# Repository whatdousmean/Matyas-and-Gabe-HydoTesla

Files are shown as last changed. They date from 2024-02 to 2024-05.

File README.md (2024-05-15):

# HydroTesla - Gabe Syring and Matyas Velgersdyk - May 15, 2024
Figure 1 - Final Product

Figure 2 - Water Board
WaterBoard
Figure 3 - Main Circuit
MainCircuit
Figure 4 - Photoresistor Headlights
Headlights
Figure 5 - Full Circuit (Main, photoresistors, and LED circuit all combined)
FullCircuit
Figure 6 - Back axel connected to gear shaft and motor
BackAxel
Figure 7 - Circuit Schematic
CircuitSchem
Figure 8 - LED Circuit
LED
Figure 9 - Battery
battery
Figure 10 - Battery Plug
batteryconnect
Figure 11 - Battery Holder
batteryPlace
Figure 12 - Finished Chassis
chassis
Figure 13 - Front Axel
frontAxel
Figure 14 - Motor & Custom Motor Holder
motor
Figure 15 - Servo
servo
Figure 16 - Blueprint
blueprint

# Design Summary
This is a car that is powered by a 12 volt battery. The battery current flows through a mosfet gateway, that can be opened by the 12 pin on an arduino uno being powered. That 12 pin is powered when our water board is put into water, stored in a tupperware container near the center of the car. That water board sends a signal back to the A0 pin on the arduino. If that analogRead value is over 150, the 12 pin will be powered, allowing the circuit to be completed, powering our 12 volt motor. This motor is connected to a simple gear system near the back of the car that is also attached to our back axel. When the motor turns, so does the axel. At the front of the car, there are two "headlights". These "headlights" are mini photoresistor circuits. Both of these circuits are powered through 5 volt pins on the arduino, and they feature voltage dividers. These voltage dividers split the current to ground and an analog pin. These two pin values are read, and then transferred into a servo. This servo is connected to our specially designed front axel, capable of performing front-steering based off of the direction of the servo. The arduino is coded to specific standards with these photoresistors. The requirements for the servo to turn are as follows: 
1) The motor must be running (The water board must be in water).
2) The analogRead value returned by one photoresistor circuit must be higher than the other.
3) The value must be higher than 150.

If all of these requirements are met, the servo will turn to either 57.5 or 122.5 degrees. This is determined by if the photoresistor is on the left or right. Otherwise, the servo remains at 90 degrees, allowing for the car to be straight. Finally, when the water board is active, it also activates the 9 pin on the arduino, turning on a green LED on the top of the car. This is just a signal showing that the car is on.

# System Details
## Main Circuit
The main circuit features a mosfet gateway that is activated from pin 12. Pin 12 is turned on by the analogRead function coming from the water board. Our circuit also features other small things, like resistors and a diode. A picture of the main circuit with the headlights and LED connected can be found in **Figure 5**.
## Water Board
Our water board is attached to the A0 pin. This pin gets a value from the water board through the analogRead() function. If the analogRead value is over 150, it activates the 12 pin, turning on the mosfet gateway. This allows the circuit to be completed, and the motor to move. The motor makes the car move because it is connected to the back axel via a gear system. A picture of the water board can be found in **Figure 2**.
## Motor
Our motor is powered through our main circuit once the mosfet gateway is activated. It is located underneath the car. We designed a custom motor holder for this, and used zipties and screws to hold it in place. A picture of the motor, gear shaft, and back axel can be found in **Figure 6**.
## Photoresistor Headlights
Our photoresistor headlights have a voltage divider on the back end of them. This splits the voltage to ground and to an analogRead() pin (Pins A1 and A2). If either these values are above 150, the 3 pin will activate using the myservo.write() function, turning the servo to the desired degree. A picture of the headlights can be found in **Figure 4**.
## Servo System
Once the 3 pin sends the servo a signal through the myservo.write() function, the servo turns to the desired degree. (For our project those degrees are 90, 57.5, and 122.5).
## LED Circuit
When the water board is activated by water, the 9 pin is turned on. This is connected to a simple LED circuit. It's only purpose is to be an on/off indicator. A picture of the LED circuit can be found in **Figure 8**.
## Battery
We used a 12 volt battery, found in the robotics lab. We used anderson power pole connectors to connect the battery to the circuit, and electical tape to secure the connection. Pictures of this can be found in **Figures 9, 10, and 11**.
## Wiring Diagram
**A detailed schematic of our wiring systems can be found in Figure 7**

# Design Evaluation
  ## Output Display 
  We used a singular green LED on the top of the car to show if it was on or off. It is powered by the 9 pin, which is turned on when the water board is dipped in water.
  ## Manual User Input 
  Our manual user input is in the form of our photoresistor headlights. The user shines a light at either of the headlights, and the car will turn towards the light.
  ## Automatic Sensor 
  Our water board automatically senses if there is water on it or not. If there is, the water board will activate our 12 volt motor and green LED. If not, the car will remain stationary and the LED will be off.
  ## Actuators 
  We used two different actuators, our servo, which activated our front steering, and a 12 volt motor, which powered the back axel to spin, and thus, the car to move.
  ## Mechanisms 
  Our two main mechanisms were our gear shaft that connected our motor to the back axel, and the servo's connection to the front axel to determine steering.
  ## Hardware 
  We had lots of different hardware, so here are all of the items: Arduino uno, plywood, screws, bolts, axels, wheels, motor, servo, tupperware, wires, CUSTOM 3D PRINTED MOTOR HOLDER, resistors, photoresistors, mosfet, LED, water board, breadboard, CUSTOM PRINTED GEARS

  Link to gear STL file: https://github.com/whatdousmean/Matyas-and-Gabe-HydroTesla/blob/ece42019ce43cfadcfe1f235608ce2f768c4addd/Main%20Gear.stl
  ## Logic, Processing, and Control
  Our full Arduino Uno code can be found here:
  
  https://github.com/whatdousmean/Matyas-and-Gabe-HydroTesla/blob/e636a06a375cc82a635ebf0bc8ff4fe23f6c6746/Water%20Board%20Arduino%20Code

  Our arduino uno was the main part of this entire project. It enabled everything, the water board, motor, photoresistors, servo, and more to work together. It is important to note that we imported the Servo library into our code in order to be able to use our servo properly. This line where we import the Servo library is on line 2 of our code. 

  ## Other Adjustments
  We did not have very many adjustments to our final plan, just two main ones:

  1) Originally, we had planned to add another photoresistor to determine speed. Unfortunately, we had to cancel this plan due to already low speeds and high resistance from the photoresistor.
  2) While this may not be a real "adjustment" this is important. We designed a custom motor holder that we installed underneath the car. This holds our motor steady and in place. The link to the stl file of this can be found here:
     
     https://github.com/whatdousmean/Matyas-and-Gabe-HydroTesla/blob/3997745cd45f1ab076b2cb9a97db56c113268df8/Custom_Motor_Holder.stl

## Construction, Quality, Aesthetics, and Visual Appeal

We worked down to the last minute on this project, and unfortunately did not have time to make it look very nice.

## Level of Effort

We put numerous out of class hours into this project, and worked down to the very last minute on it. We think we will get extra points for this.

## Cost

Our cost is below $100. We think we will get the extra points for this as well.

# Lessons Learned

Our main lesson that we learned is to be calm. At many points, we got very frustrated. This hindered our work time usage, mood, and overall production. We had many issues building our circuits and getting everything to work together. In the end, staying calm and trying new methods is what enabled us to finish on time. 

Throughout this project, we learned that planning how to use your time is very important. Time flies when you are so focused on something. The class periods went by a lot faster than we expected.

Biggest Suggestion: Plan out your class periods, when you expect to have certain things done by, and stick too it. In February it seemed like we had all the time in the world. Time flies with this project. Stay calm when working, and don't give up.

# Parts List
-Wheels: 8.99 https://www.amazon.com/Electric-Geared-Magnetic-Gearbox-Plastic/dp/B098PZF2DV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

-Tupperware: 4.99 https://www.amazon.com/GladWare-Everyday-Rectangle-Storage-Containers/dp/B0085UK4GW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

-Nuts, Bolts(1/4 inch diameter, 2.5 inch length, 13 count), Washers and Axel : Aprox. 17.50 (Tax Included) at Ace

-Plywood: 10.00

-12 Volt Motor: 14.99 https://www.amazon.com/Greartisan-Electric-Reduction-Centric-Diameter/dp/B07K9KPDNV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

-Arduino: 15.00

-General Electronics(Including Servo, Water Board, and Battery): Aprox. 20.00
	- 4 220 Ohm resistors, mosfet, diode, LED, breadboards

-3d Prints: Motor Casing (50 grams) Beveled Gears (29 grams)

### Total: $91.47
## Other Parts
- Wires
- 3D Printer
- Arduino app
- Connection cords
- Electical tape
  
# Assembly Instructions
If you want to build this, follow these instructions!
## Electronics
The electronic and coding portions of this project are very complicated. Start by copying our code (In logic, processing, and control) over to your arduino script. Also make sure you have all the materials listed. You will need many male to male and male to female wires for this. 

### Circuits
In **Figure 7**, you can see all of the circuit's wiring. Start by building all of these circuits. Put the main circuit on a big breadboard, and the other 3 on mini breadboards. The servo and waterboard do not need a breadboard, you can directly connect them. Make sure to not take off the bottom stickers to these breadboards yet. Throughout building these parts, make sure you are testing voltage and amperage levels with a multimeter. All of this, including the arduino should be powered by the 12 volt battery. Tip: Connect the main power from the battery to the + strip on the main breadboard. From there, power the arduino and the rest of the circuits from the arduino. You will most likely need an arduino shield to have enough ports. A picture of our final circuit can be found in **Figure 5**.

## 3D Printed Parts
We used OnShape to print our **3** custom parts. Download our STL files above and 3D Print these parts. (You will need to print two of the gears).

## Chassis (Main Body), Servo, and Axels

### The chassis blueprints can be found in **Figure 16**.

Before the chassis was constructed, it was planned out on a 3d modeling software used by Geomatic Engineers, colloquially called Surveyors, known as Autodesk Civil 3d. The chassis was modeled after a Ford F150 outline from the top, and although plans were made to make layers to build out the full body shape of the Ford truck, that was never done as it would have taken far too long. Instead, 2 layers, identical for the most part excluding some minor changes surrounding the front wheel wells, and the motor-casing attachment point and cutout. 

After the chassis was designed, it was printed full-scale onto a sheet of paper, and traced onto a sheet of plywood. It was then cut out, excluding the cutouts for the motor casing and the water tank(tupperware container) making use of a scroll saw. After that was done, holes were drilled for support posts between the two chassis layers (the bolts), and the first assembly was done. These bolts at the time were 1.5 inches in length, but after being discovered to be too short later on, they were changed to be 2.5 inches long. In any case, once this was done, focus switched to the steering mechanism and the back axel. 
	
The steering mechanism is made up of two thin cutouts of plexiglass spanning across two free-spinning armistices(a y-shaped aluminum object with a bearing) holding the wheels onto a fixed point, which will be explained in more depth during the presentation. These are then connected to a servo using more free spinning attachment points, to enable easy rotation, and precise control. This was made using the scroll saw and the drill press over the course of a couple of class periods, and was swiftly assembled. The rear axle was much simpler, only making use of 1 beveled gear(3d printed, model lifted from a beveled gear found in the lab) that interfaces with one attached to the motor, a dowel rod, and two wheels,  as well as two pillow blocks to keep the axle in place. To attach the wheels to the axel, the gear was first slid onto the dowel rod after which point I stuck the axel into a hole in each wheel, which will be shown during the presentation. The aforementioned pillow blocks are sat upon a significantly raised portion of plywood, which is made by tracing the outline of the bottom of the pillow block onto a plywood sheet 4 times, and cutting these out. Then, stack them on top of one another and drive a screw through the pillow block and the stack of plywood, and then into the chassis. It’s recommended to use screws that are fairly short, as cutting them is a painful process.  WD40 was used to  lubricate the pillow blocks to reduce friction on them, but that was all. After this, the cutouts in the chassis were made using the drill press and chisels, and the motor casing and water tank were then attached, leaving one final step, which was to insert the electronic components, thus completing the build process. The motor was attached using a 3d printed casing, that was then nailed into the chassis, and held down using zip ties. The servo was affixed making use of wood screws going through two little wings on it’s sides and the chassis, holding it in place. Zip ties were added later to  add stability. 

To build the chassis, take your plywood and form it to the specifications of the blueprint in Figure ?. This takes a while, but it will be worth it in the end. After you have your 2 pieces of wood, you can begin connecting them with the nuts, bolts, and columns as seen in **Figure 1** and on the blueprints. Throughout the rest of the assembly, you will be taking the two pieces apart and putting them together multiple times. A picture of the finished chassis can be found in **Figure 12**.

A picture of the front axel can be found in **Figure 13**, and a picture of the installed servo can be found in **Figure 15**.

## Motor & Motor Holder
At this point, you should have your custom printed motor holder. Take your actual motor and slide it in. After this, strip two wires and wrap it around the motor's positive and negative extensions. We used electrical tape to secure this. These two wires will link back into your circuit. Use zipties to secure the motor to the motor holder. After, the motor holder needs to be nailed to the bottom of the car in the position shown in the blueprint. This is shown in **Figure 14**.

## Tupperware
This part is not complicated. Take the lid of your tupperware, and cut a slit in the middle of it big enough for the water board to fit in. In the end, your waterboard will slide into this.

## Gears
For the gears, connect one to the back axel, and the other to the part of the motor that sticks out. Slide these around until they connect. After that, you can superglue them to the axel and motor. This will make your gear shaft.

## Battery Pack
Near the back of the chassis, you will find two small holes. These are designed to have zipties go through them. Take your two zipties, and tie down the motor here. Get yourself an anderson power pole connection for the connection into the breadboard. Pictures of this can be found in **Figures 9, 10, and 11**.

## Final Assembly
Now, it is time to combine everything. Take off the second piece of plywood, and install your circuit. This is where you take off the stickers of your breadboards. Your headlights go on the front of the car, your breadboard and arduino in between your tupperware and motor, and your LED and water board will go on top of the car on the second piece of plywood. These will connect to the arduino through the little holes for the wires as seen on the blueprint. Your servo will still be connected to the arduino, but it will be screwed in as stated above.

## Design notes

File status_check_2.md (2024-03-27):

2) We have done testing on our main sensor, the water board, and have been able to generate roughly 1.5 volts out of it when submerged in water. This was while it was connected to a 5 volt source.
3) We have a motor that is in the process of being ordered, and we have begun a 3D design in OnShape for a custom holder of the motor. We also have begun sketching out a model for our main platform which will hold our water tank and more.
4) We have one function element that is currently working, and that is our water board. We plan to use the voltage it produces to open up a bigger, 12 volt circuit that will power the motor, and thus move the car.

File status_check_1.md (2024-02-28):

1) We have not begun constructing anything yet.
2) We have not ordered all the parts we need yet, we are looking into getting a water container, motors, wheels, and extra parts like screws.
3) We have begun thinking about 3D printing some plates to use as floors, and designing them to custom fit our parts.
4) (Output - LED showing on/off, speed displaying on screen)
  (Manual User Input - Code telling car when to turn, Light on photoresistor, amount of water)
  (Automatic Sensor - Photoresistor adding or subtracting to voltage levels depending on light)
  (Actuator - Motor on wheels, Mechanisms - Photoresistor contributing to voltage levels, water sensor contributing to voltage levels, Hardware -       
  Gears, wiring, 3D prints, screws)
  (Logic - Arduino, Raspberry Pi, motor board code)
5) The three hardest parts of this project will be getting a water container that wont spill water everywhere, wiring up the transistor to the water board and photoresistor, and figuring out a way to possibly put a light directly over the photoresistor to vary energy levels

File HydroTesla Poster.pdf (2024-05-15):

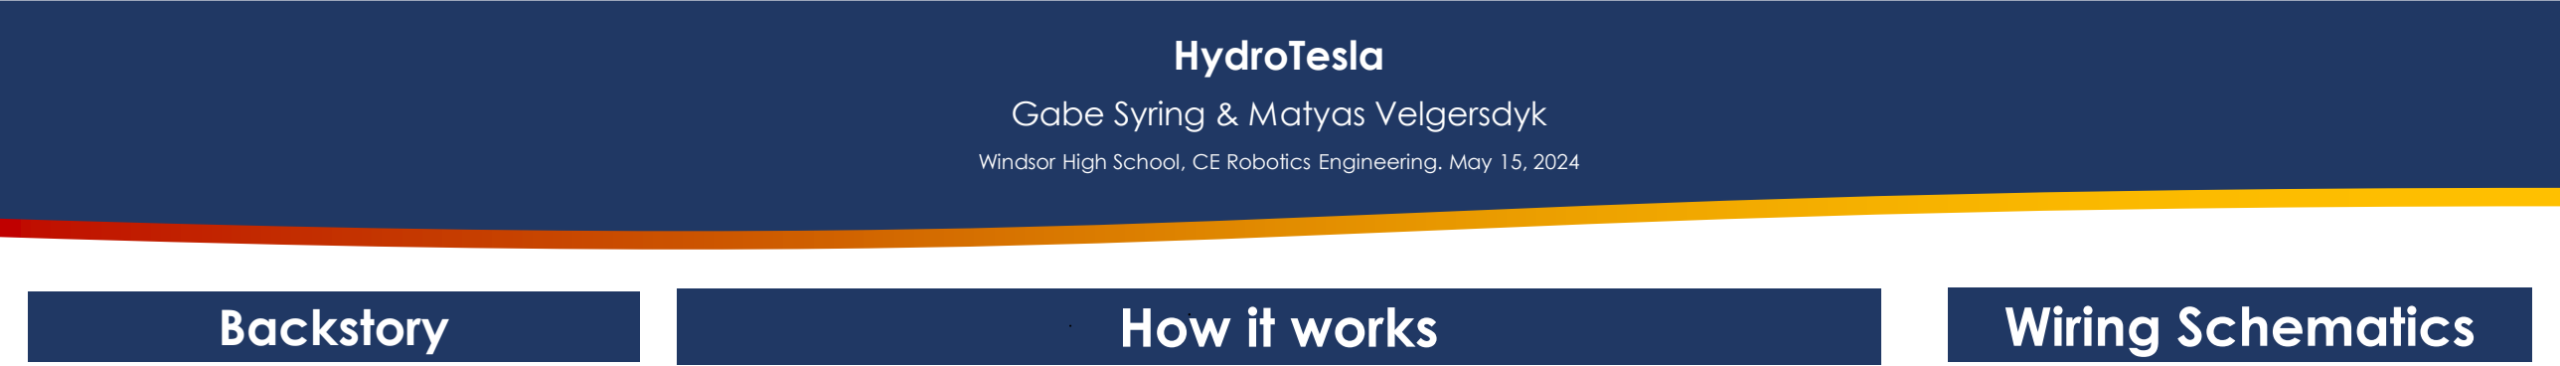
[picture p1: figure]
Backstory; How it works; Wiring Schematics; Gabe Syring & Matyas Velgersdyk; HydroTesla
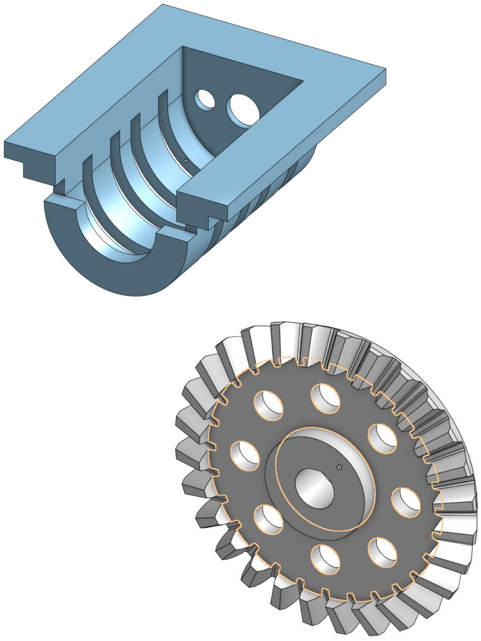
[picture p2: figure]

RESEARCH POSTER PRESENTATION DESIGN © 2022
www.PosterPresentations.com

Initially, we had two project ideas: a water powered car, and a railgun. We decided to go with the water powered car (now named HydroTesla) mostly because a railgun would not be safe to work on in a school. Although a railgun would have been super fun, there is no way it would've been approved. We anticipated that this would be a big challenge, and it definitely was. We worked down to the last day on this project.

# Custom Prints

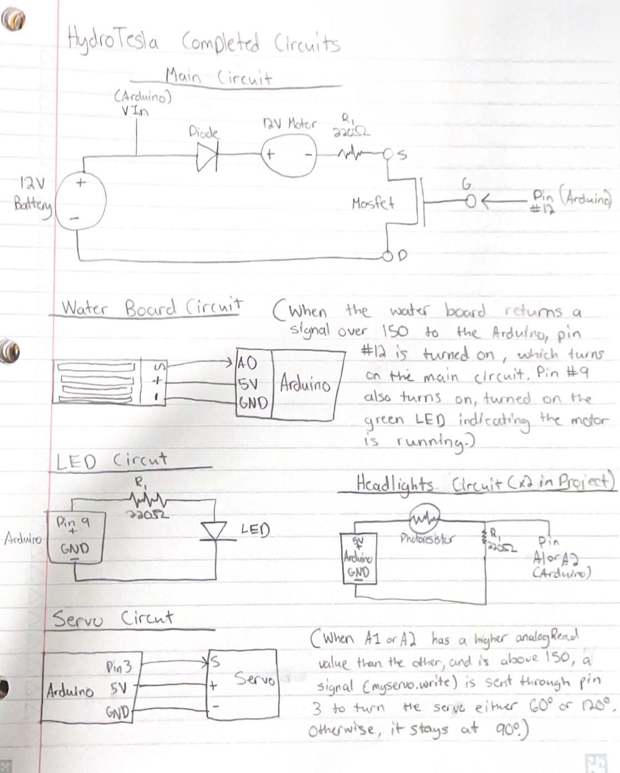
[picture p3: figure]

# Conclusion

Overall, we had lots of fun with this project. It for sure was a challenge, but we know that from the start. There were many points where we didn't think we would finish in time. Sometimes we didn't think it was possible. Multiple wiring components were overheated and destroyed. Mistakes were made, but in the end, they were for the better. We learned many lessons during this project, but two stood out to us:
- Always believe in yourself
- Stay calm, otherwise you won't think straight or get any work done

To future students, our advice is this:
- Plan out deadlines and dates, and stick to them. Do not put anything off until the last minute
- Keep a calm head. Getting angry doesn't help

We used OnShape to design and print 3 custom parts. A custom motor holder to stabilize our motor, and 2 gears to create our gear system. Combined, these custom parts allowed our car to move.

Windsor High School, CE Robotics Engineering. May 15, 2024

The water board sends an
analogRead signal back to
the arduino, and if the signal is

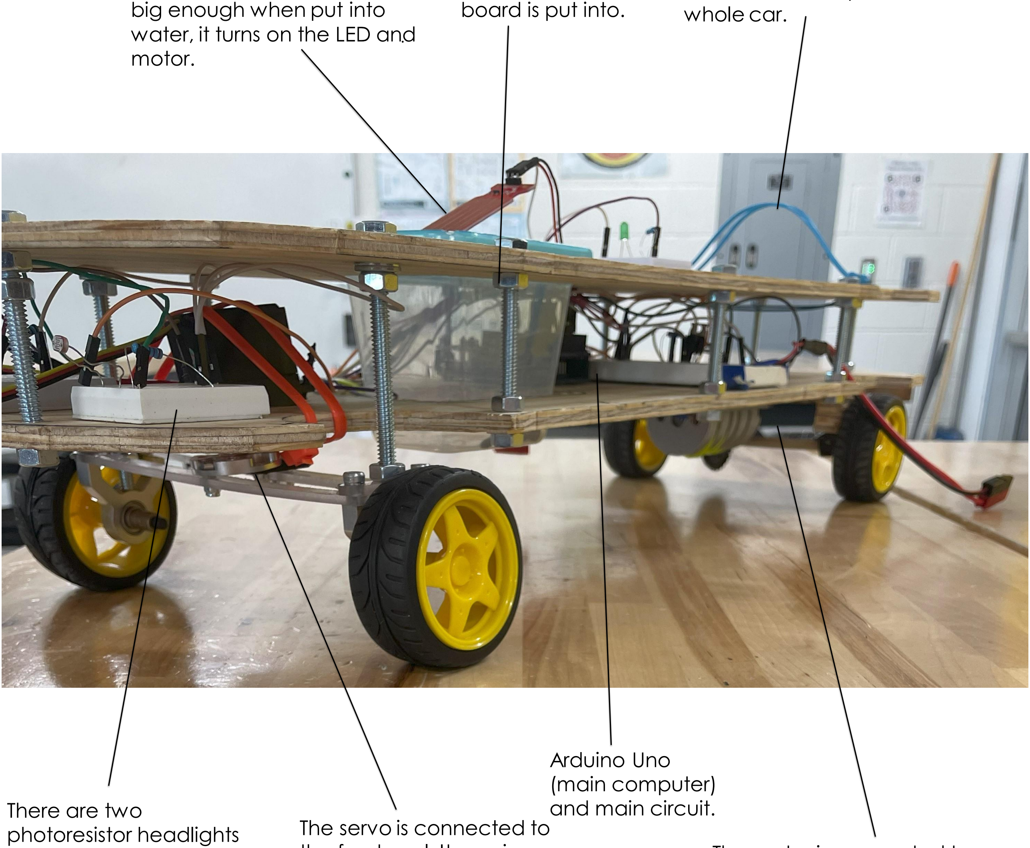
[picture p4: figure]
water, it turns on the LED and motor.; whole car.; There are two photoresistor headlights; The servo is connected to; board is put into.; Arduino Uno (main computer) and main circuit.

big enough when put into

The battery is held here, and it is connected to the breadboard via Anderson PowerPole
Connectors. This powers the

here. They are constantly
sending a signal back to
the arduino board. The
signal goes up when a
light is flashed at it. If that signal is over 150 for one photoresistor, the car will turn towards the light.

the front axel. It receives a signal from the arduino, telling it what to do and
where to move. This is
how the headlights
control the steering,
because they send a
signal to the arduino that is then sent to the servo.

The motor is connected to our gear system, which is connected to the back axel. When the motor is activated by the water board, the motor spins. This spins the gear system, which makes the back axel turn. This is how the car moves!

Water Tank
where water

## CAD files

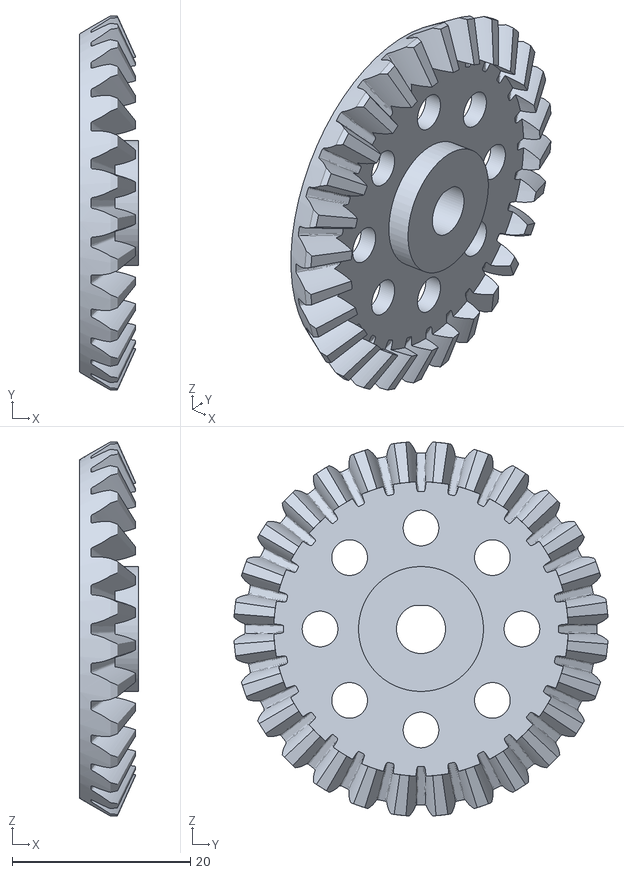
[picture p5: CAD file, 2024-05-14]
Main Gear.stl
6.61 x 41.9 x 41.9

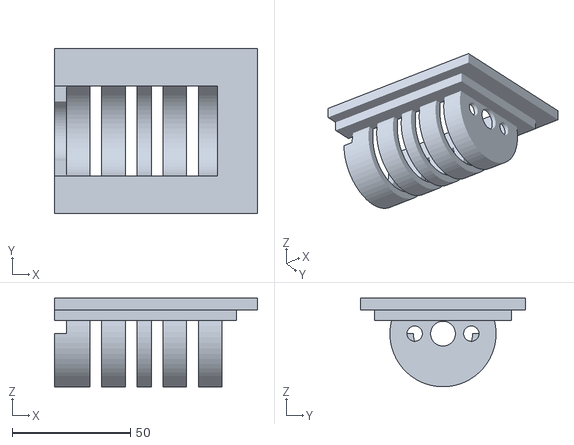
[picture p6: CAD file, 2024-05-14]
Custom_Motor_Holder.stl
86.0 x 70.0 x 37.5

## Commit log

2024-03-29 Create Water Board Arduino Code
2024-03-29 Update Water Board Arduino Code
2024-05-14 Rename Motor Holder.stl to Custom_Motor_Holder.stl
    [Custom_Motor_Holder.stl]
